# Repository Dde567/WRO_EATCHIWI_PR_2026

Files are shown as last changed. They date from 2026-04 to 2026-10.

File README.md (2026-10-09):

# WRO_EATCHIWI_PR_2026

This repository contains the documentation of the team EatChiwi on the challenge of creating a self-driving vehicle. Here you're going to find all about the creation of the vehicle: mechanical parts, programation, and system thinking. 

Our Ticket to the Internationals! (2026)
===

<div align='center'>
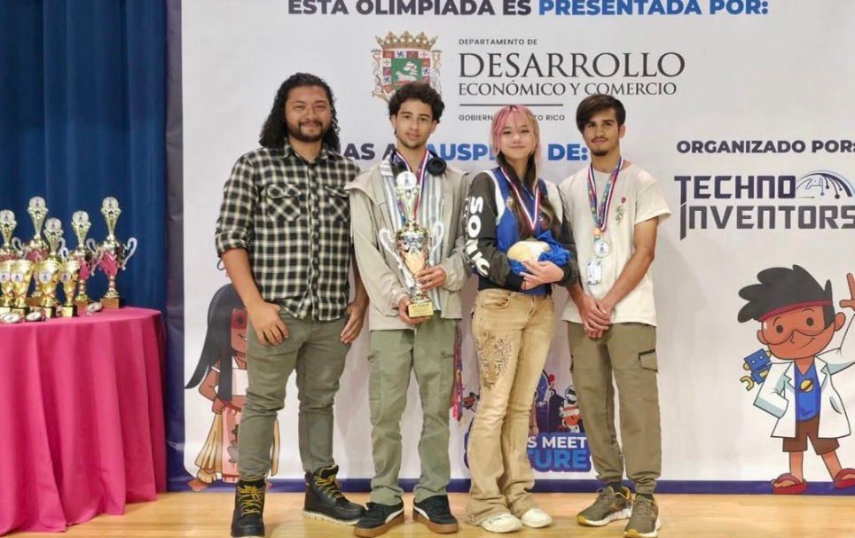
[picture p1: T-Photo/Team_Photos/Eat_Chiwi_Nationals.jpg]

</div>

## Introduction:

Welcome to Team EatChiwi, competing in the Future Engineer's category! Our challenge is to design and program a self-driving car. While building the hardware from scratch wasn't a requirement, we wanted to push our limits. We designed, manufactured, and assembled our entired vehicle from the ground up using 3D printed materials, running on our own custom software. In this process, our dedication was the key to keep pushing forward. In this repository, you'll find our story, our background, and learn more about the whole process of how we create our vehicle. 

<div align='center'>

### <U>[Table of Content!](#table-of-content-)</U>
</div>

Team Photo (from left to right)
===
- Efrain Ortiz (18) - current freshman (college) and our trusted mechanic. Responsible of the creation of the models of the vehicle and the car itself. He's a real innovator and main strategist.
- Faneshka Cartagena (18) - current senior and is the person dedicated to take note of everything. She's a very dedicated and creative person. Responsible of all the documentation of the creating and thinking process. 
- Jose Ortiz (17) - current senior and the programmer of the group. Responsible of the creation of the program of the vehicle and the one in charge to make the strategy come to life.
<div align='center'>
<table>
    <tr> 
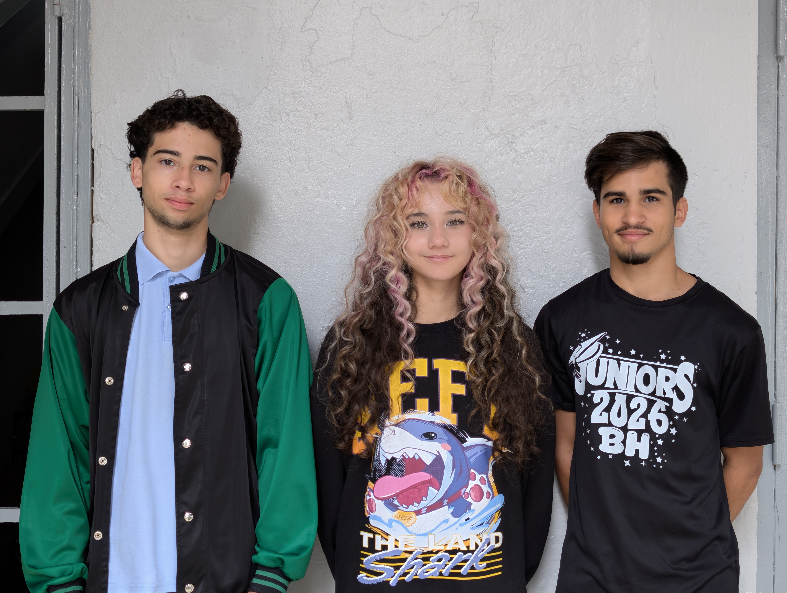
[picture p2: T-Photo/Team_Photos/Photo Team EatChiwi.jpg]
A detailed description of the photo
        <td> 
        </td> 
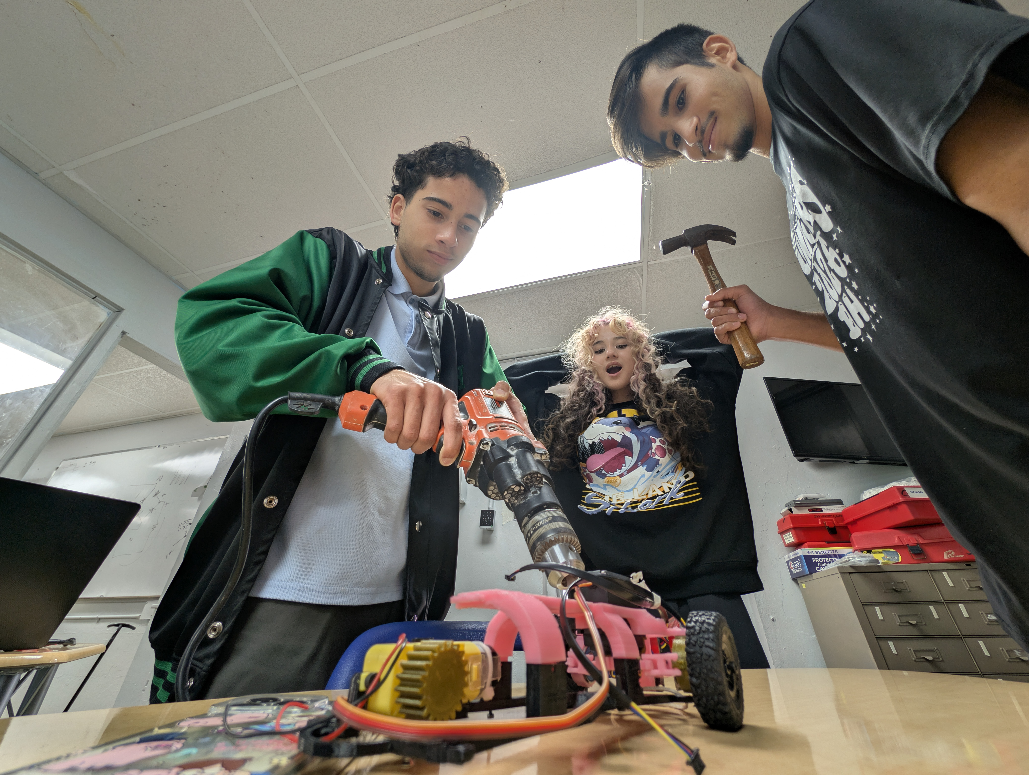
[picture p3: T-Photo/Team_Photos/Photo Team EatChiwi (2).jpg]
        <td> 
        </td>
        </tr>
    </table>
</div>

### <div align='center'> <U> [Learn more about us!](T-Photo\README.md) </U> <div>

Our team's Mascot!
===
Meet our team’s mascot, Chisgüys herself, our lucky charm!
(Ignore what we’re working on in the back.)

<div align='center'>
<table>
    <tr> 
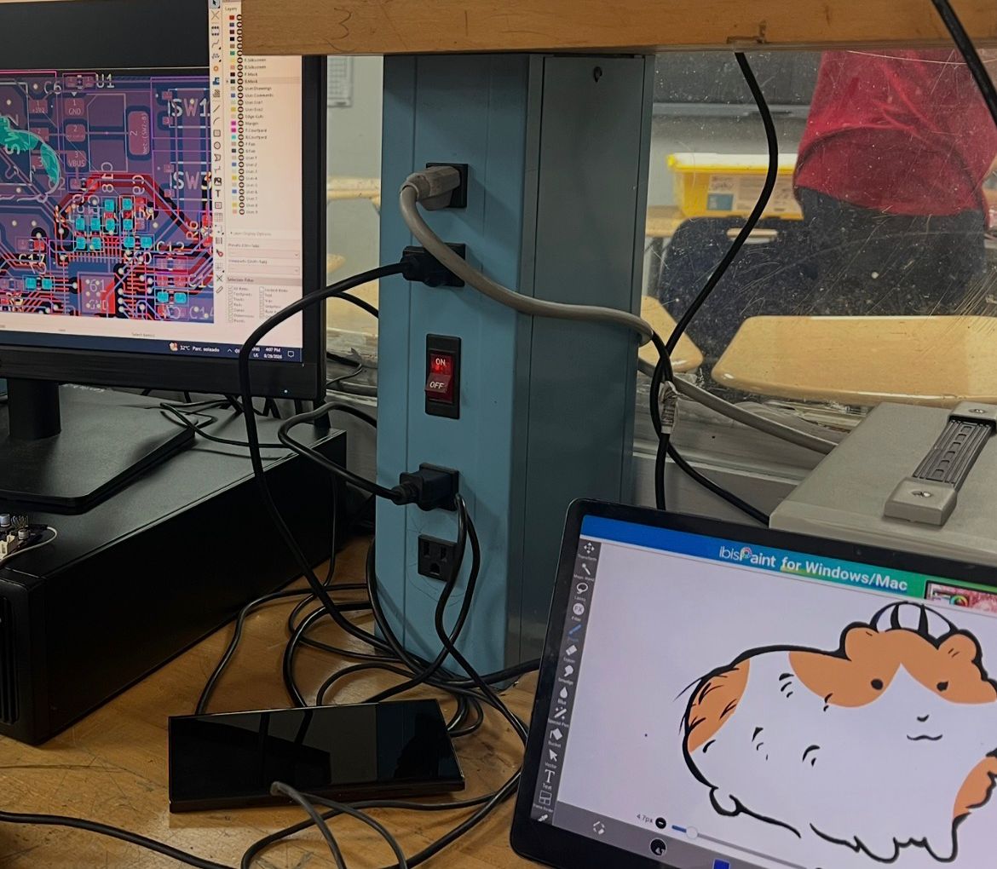
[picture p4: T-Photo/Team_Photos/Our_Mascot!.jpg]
A detailed description of the photo
        <td> 
        </td> 
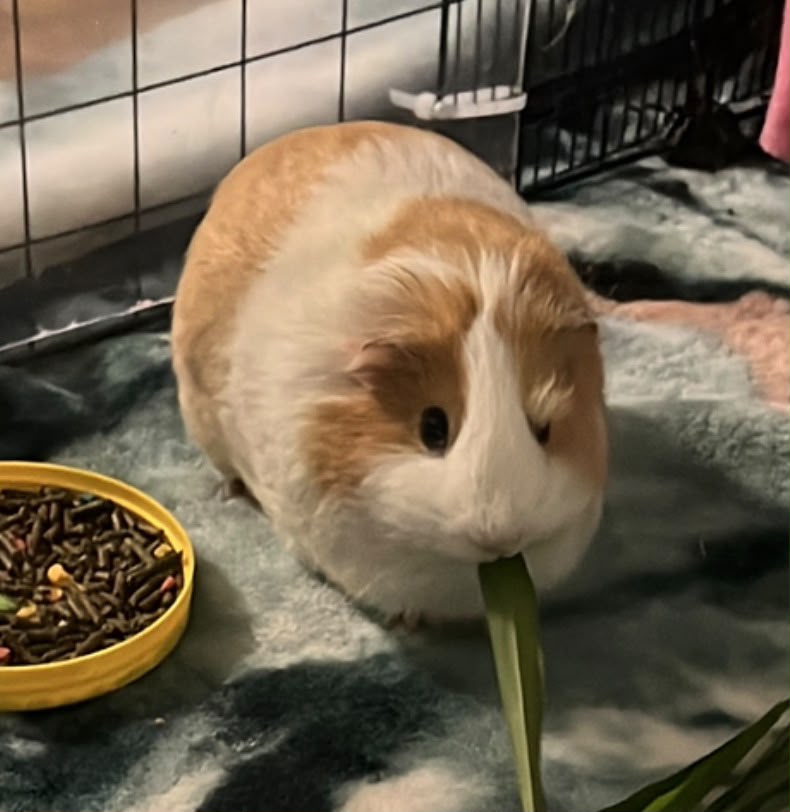
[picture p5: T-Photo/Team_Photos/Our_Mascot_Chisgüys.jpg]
        <td> 
        </td>
        </tr>
    </table>
</div>

Vehicle Photo
===
## V-1.5 (Sept/12/26)
<div align='center'>
<table>
    <tr> 
        <td> <div style="position: relative; display: inline-block;">
        <!-- Image -->
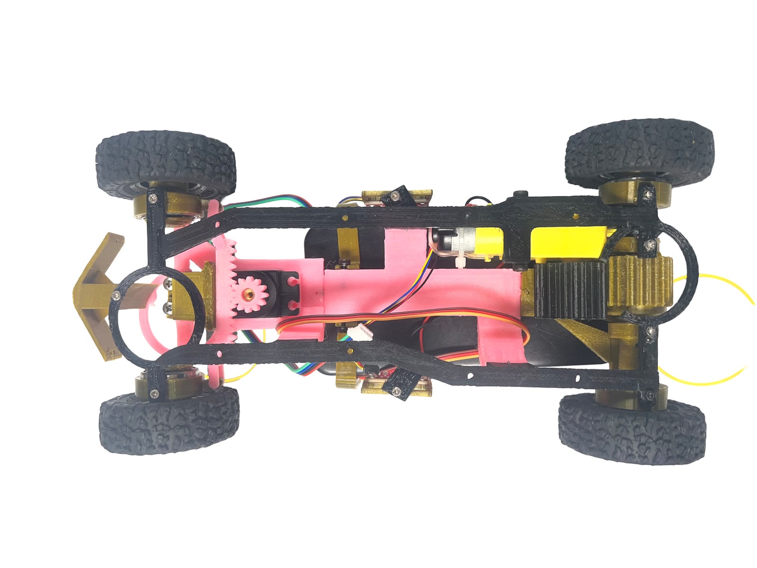
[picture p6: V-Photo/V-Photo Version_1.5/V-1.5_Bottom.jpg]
         
  <!-- The Text Overlay -->
  <div style="
    position: absolute; 
    top: 10px; 
    left: 10px; 
    background-color: rgba(0, 0, 0, 0.79); 
    color: white; 
    padding: 8px 12px; 
    font-family: sans-serif;
    border-radius: 10px;">
    <b> Bottom </b>
  </div>
</div>
        </td> 
        <td> <div style="position: relative; display: inline-block;">
        <!-- Image -->
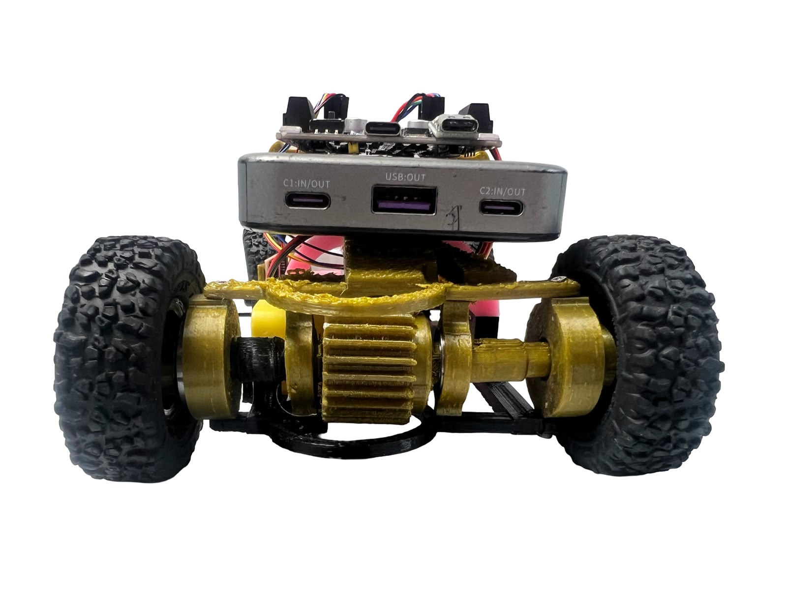
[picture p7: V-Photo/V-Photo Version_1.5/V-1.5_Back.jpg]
         
  <!-- The Text Overlay -->
  <div style="
    position: absolute; 
    top: 10px; 
    left: 10px; 
    background-color: rgba(0, 0, 0, 0.79); 
    color: white; 
    padding: 8px 12px; 
    font-family: sans-serif;
    border-radius: 10px;">
    <b> Back </b>
  </div>
</div>
        </td>
        <td> <div style="position: relative; display: inline-block;">
        <!-- Image -->
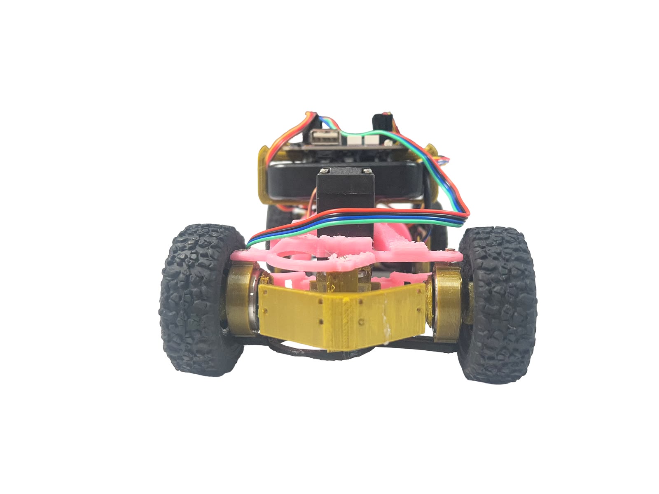
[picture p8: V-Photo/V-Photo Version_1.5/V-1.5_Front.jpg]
         
  <!-- The Text Overlay -->
  <div style="
    position: absolute; 
    top: 10px; 
    left: 10px; 
    background-color: rgba(0, 0, 0, 0.79); 
    color: white; 
    padding: 8px 12px; 
    font-family: sans-serif;
    border-radius: 10px;">
    <b> Front </b>
  </div>
</div>
        </td>
    </tr>
    <tr> 
        <td> <div style="position: relative; display: inline-block;">
        <!-- Image -->
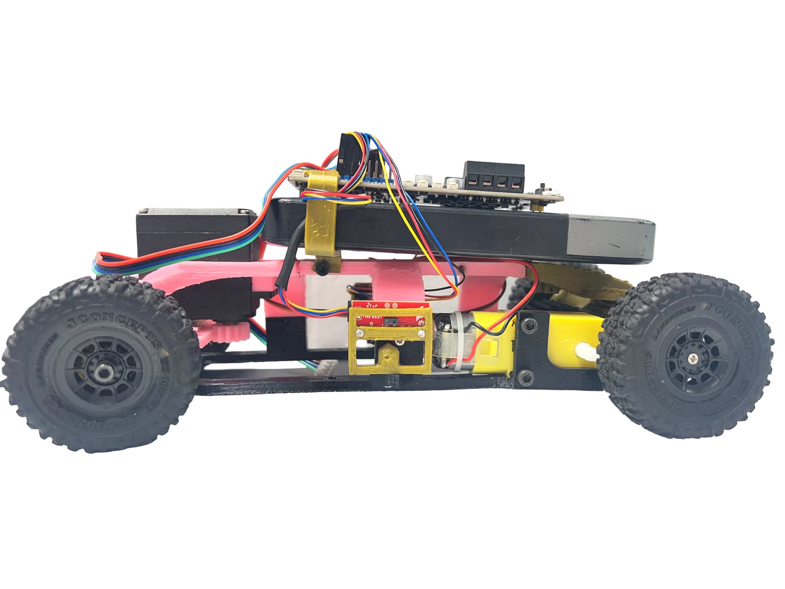
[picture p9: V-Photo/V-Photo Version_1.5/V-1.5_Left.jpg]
         
  <!-- The Text Overlay -->
  <div style="
    position: absolute; 
    top: 10px; 
    left: 10px; 
    background-color: rgba(0, 0, 0, 0.79); 
    color: white; 
    padding: 8px 12px; 
    font-family: sans-serif;
    border-radius: 10px;">
    <b> Left </b>
  </div>
</div>
        </td>
        <td> <div style="position: relative; display: inline-block;">
        <!-- Image -->
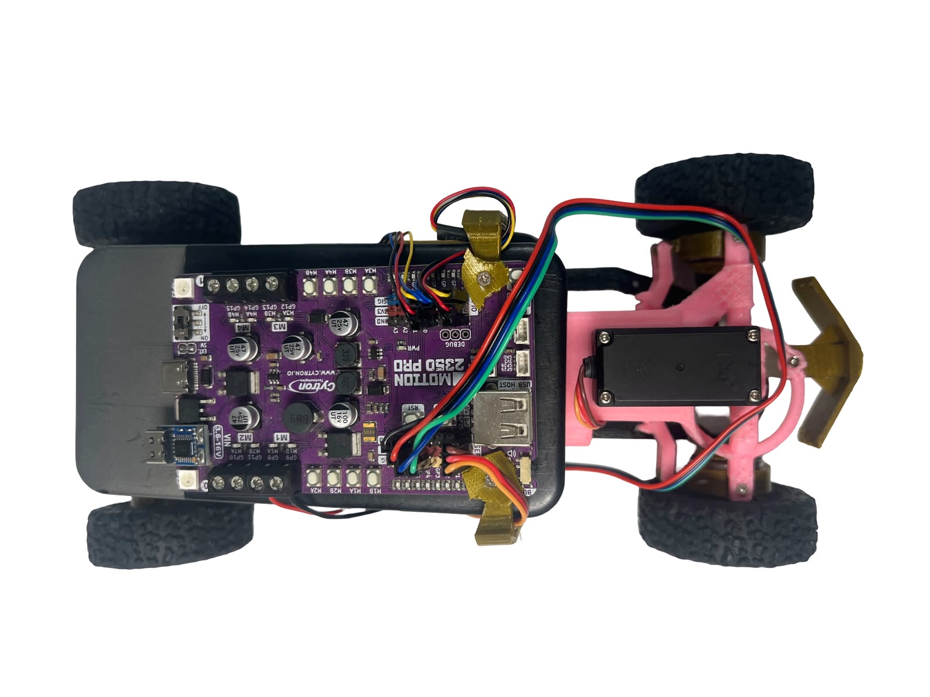
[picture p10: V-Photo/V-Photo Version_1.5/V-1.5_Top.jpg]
         
  <!-- The Text Overlay -->
  <div style="
    position: absolute; 
    top: 10px; 
    left: 10px; 
    background-color: rgba(0, 0, 0, 0.79); 
    color: white; 
    padding: 8px 12px; 
    font-family: sans-serif;
    border-radius: 10px;">
    <b> Top </b>
  </div>
</div>
        </td>
        <td> <div style="position: relative; display: inline-block;">
        <!-- Image -->
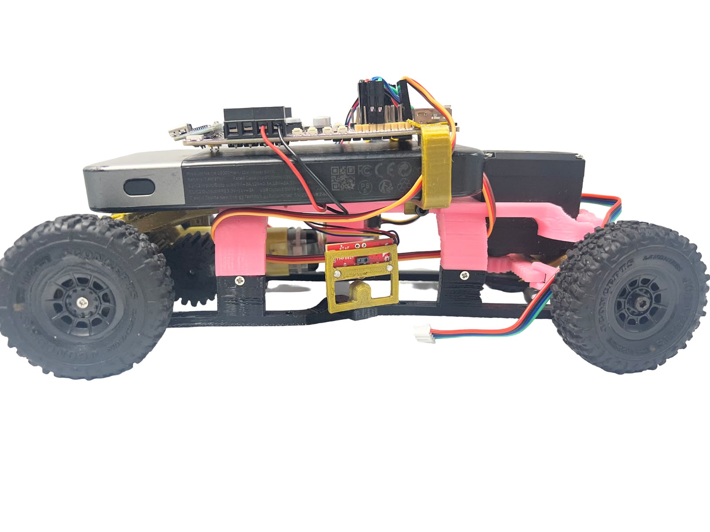
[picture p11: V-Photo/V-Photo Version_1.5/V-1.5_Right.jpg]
         
  <!-- The Text Overlay -->
  <div style="
    position: absolute; 
    top: 10px; 
    left: 10px; 
    background-color: rgba(0, 0, 0, 0.79); 
    color: white; 
    padding: 8px 12px; 
    font-family: sans-serif;
    border-radius: 10px;">
    <b> Right </b>
  </div>
</div>
        </td>
    </tr>
    </table>
  </div>

## About the Mechanics:

The design of the car it's a compact design created in this way to be more quicker to print and more easy to avoid obstacules. The measurements of the car are: lenght = 25cm, width = 11.5cm, tall = 9cm. The car is RWD drived by a TT motor and a MG996r servo motor for steering. The brain of the car is the microcontroller MOTION PRO RP2350. The car counts with 4 wheels of 51mm, 2 TCS3472 on front, 2 TMF8821 on front, TMF8821 sensors on each side and will have a BMI270 for orientation. On the top, just below the microcontroller it's the battery that have a capacity of 37W/h and can supply 35W continuos and counts with a capacity of 10,000mAh.

## About the Code:

Our robot is an autonomous robot programed to complete the Future Engineer's track. To program the robot, the IDE we use is Thonny. To create the code we're using different libraries and sensors:

- `tmf8821` - EJOM CODE @Dde567
- `servo` - EJOM CODE @Dde567
- `dcmotor` - [dcmotor.py](Code-Development/lib/dcmotor.py)
- `tcs3472` - [tcs3472.py](Code-Development/lib/tcs3472.py)

To upload the code to the microcontroller: connect the microcontroller to your computer using a USB cable. Turn it on, then open your IDE (in our case, Thonny) and make sure the microcontroller is recognized. Press the right click on the program you want to upload and select save. Once saved, the code is successfully uploaded to the microcontroller.

## Table of Content :

| Type | Content | Readme |
|---|---|---|
| Mechanics | [CAD](Mechanics/CAD) | [Mobility and Mechanical Design](Mechanics\README.md)|
| Electrical-Design | [Hardware CADS](Electrical-Design/HardwareCADS) / [Electrical Diagram](Electrical-Design/Electrical_Diagram.png) | [Power and Sensor Architecture](Electrical-Design\README.md)|
| Code-Development | [Lib](Code-Development/lib)| [Software Architecture and Obstacle Stategy](Code-Development\README.md) |
| T-Photo | [T-Photo_Normal](T-Photo/Team_Photos/Photo%20Team%20EatChiwi.jpg) / [T-Photo_Crazy](T-Photo\Team_Photos/Photo%20Team%20EatChiwi%20(2).jpg) | [Our Team!](T-Photo/README.md) |
| V-Photo | [V-1.0](V-Photo/V-Photo%20Version_1.0) / [V-1.1](V-Photo/V-Photo%20Version_1.1) / [V-1.2](V-Photo/V-Photo%20Version_1.2) / [V-1.3](V-Photo/V-Photo%20Version_1.3) / [V-1.4](V-Photo/V-Photo%20Version_1.4) / [V-1.5](V-Photo/V-Photo%20Version_1.5)| [Versions of the Car](V-Photo\README.md) |
| Video | [Open Lap for PRNRO 2026 (Team EatChiwi)](https://youtu.be/rVMPH4gbWxk?feature=shared) |||

<div align='center'>

#### <u>[Back to the top!](#wro_eatchiwi_pr_2026)<u>
</div>

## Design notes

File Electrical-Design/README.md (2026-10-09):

# Electrical Design 

In this document you'll find all the things about the electrical components like the capacity of the sensors, the battery, and how is designed the electrical on the robot.

## Introduction
Our electrical design consists of the amount of 8 sensors, with which our car is capable of flawlessly driving through the track without much difficulty. The sensors of our choice are: 2 TCS3472-TMF8821 sensors on the front for effective color detecting and distance reading, some TMF8821 distance sensors on each side for mantaining the car as centered through the track, a HuskyLens 2 camera in the front for better color detection, and lastly our BMI270 IMU which we will use to make the car know where it is at and where is headed to. The powerful brain here is a MOTION PRO RP2350 which programmed in micropython is more than capable of handling every sensor on the list. Our drive hardware consists of the trusty TT motor for driving and a sturdy MG996r servo motor for steering. But this is too simple right? Just using some generic hardware to make our car drive is too basic for us engineers? Well of course, we can do more, we can do better, and thats why we are designing our own sensors for future competitions. As a matter of fact we ALREADY have the schematics for a mix of the powerful TCS and TMF sensors (designed by us) in one board and we plan on making the best hardware we can for our needs in this competence. 

## Battery
The battery it's a JUOVI power bank that has a capacity of 37W/h and can supply 35W continuos, with a capacity of 10,000mAh and includes dual USB Type-C ports and one USB-A port. 

## How much the sensors consume?
- MOTION PRO RP2350 (microcontroller) = Normal Run: Approximately 22mA.

- TMF8821 (distance sensor) = Active Current Consumption: ~57 mA.

- TCS3472 = 235mA to 330mA (operating at 3V)

- BMI270 (accelerometer + gyroscope (MaxODR)) = 685mA

- HuskyLens 2 = 1.5W to 3W (operating at 3.3V or 5.0V)

- MG996r (servo) = Operating Current (Under Load): 500mA - 900mA.

- TT motor = At 6VDC: 160mA @ 250 RPM no-load, and 1.5 Amps when stalled.

## Electrical Diagram 
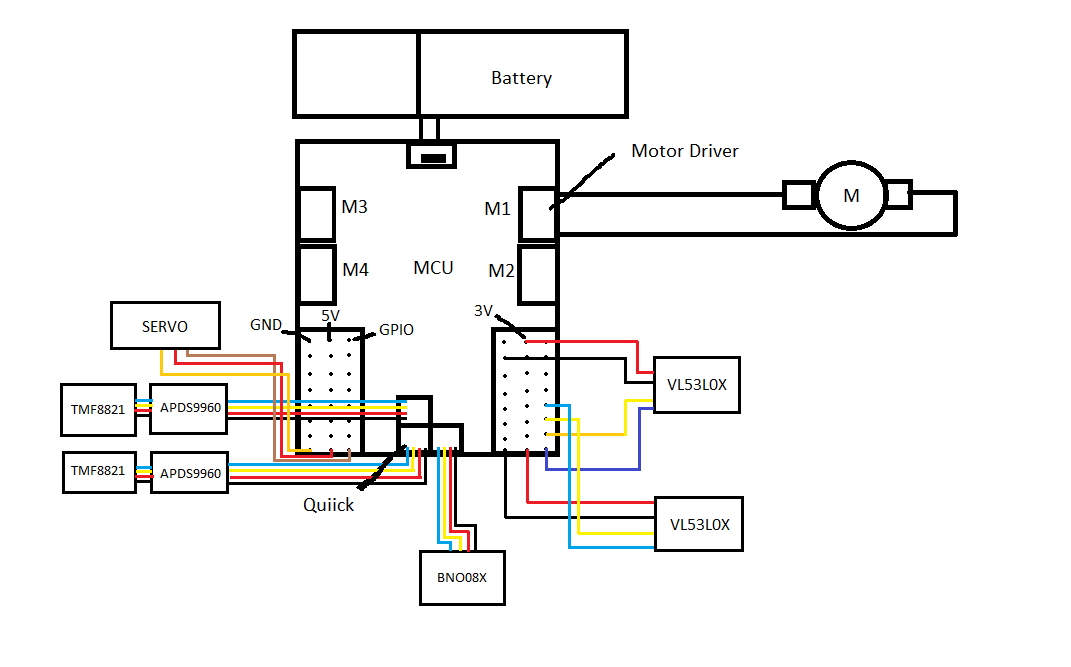
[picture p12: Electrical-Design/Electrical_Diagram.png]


## Robot Composition 

The robot is composed of 8 sensors that are distributed in all the robot. These sensors help the robot to know where he goes, what he have to do, and when he have to stop. Sensors are, in few words, the eyes, hands, and ears of the robot. 

The chosen sensors for the robot were:

| Sensor | Brief Description | Specifications | Library |
|---|---|---|---|
|TMF8821| Distance Sensor | [ams TMF8821 configurable 4x4 multi-time dToF](https://ams-osram.com/products/sensor-solutions/direct-time-of-flight-sensors-dtof/ams-tmf8821-configurable-4x4-multi-zone-time-of-flight-sensor)| [tmf8821.py](Code-Development/lib/tmf8821.py) |
|TCS3472| Color Sensor | [TCS3472 Datasheet](https://cdn-shop.adafruit.com/datasheets/TCS34725.pdf) | [tcs3472.py](Code-Development\lib\tcs3472.py) |
|BMI270| IMU Sensor |  [BMI270 Datasheet](https://www.bosch-sensortec.com/media/boschsensortec/downloads/datasheets/bst-bmi270-ds000.pdf) | [bmi270.py]()
|HuskyLens 2| Advanced Smart AI Vision Sensor | [HuskyLens](https://wiki.dfrobot.com/sen0638/) | [huskylens2.py](Code-Development\lib\pyhuskylens.py)
|Cytron Motion Pro RP2350| Microcontroller | [Cytron Motion Pro RP2350 Datasheet](https://www.cytron.io/p-motion-2350-pro?srsltid=AU7gw4W5Ifi1J22W_zTflltF3oPrDEIvFmEJ27_g_rW_nqw14TCFXhvm)

## Our System!

<table>
  <thead>
    <tr>
      <th width="20%"> Hardware</th>
      <th width="45%"> What it is?</th>
      <th width="45%"> Why we decide to use it
    </tr>
  </thead>
  <tbody>
    <tr>
      <td><b> TMF8821 </b></td>
      <td>
        <details>
          <summary> Description (Click to expand) </summary>
          <p> The ams OSRAM TMF8821 is a compact multi-zone direct Time-of-Flight (dToF) optical sensor measuring precise distances from 10 mm to 5,000 mm at up to 30 Hz. Housed in a tiny 4.6 mm x 2.0 mm x 1.4 mm package, it integrates a 940 nm Class 1 eye-safe VCSEL, a high-sensitivity SPAD array, and on-chip histogram processing to support configurable 3x3, 4x4, or 3x6 grids with a 63° field of view. Communicating over I²C, this high-performance module features sunlight immunity and dynamic cover glass calibration, making it ideal for smartphone laser autofocus, presence detection, and robotics. </p>
        </details>
      </td>
      <td>
      <details>
          <summary> Description (Click to expand) </summary>
          <p> We decide to use the TMF8821 distance sensor for the robot. Why we choose this? Well, after using other distance sensors like the  Vl53l0x and the Vl53l1x (V-1.4 and past versions), or the hcsr04 distance sensor (V-1.3 and past versions), the one who give us better results in reading distance it was the TMF8821. It ensures better lectures than the others, specifically better lectures when its time to read the black walls of the circuit. For this reason, we decided to keep and use the TMF8821 in the robot, seeking for the best lectures and more accuracy. </p>
        </details>
      </td>
    </tr>
    <tr>
      <td><b> TCS3472 </b></td>
      <td>
        <details>
          <summary> Description (Click to expand) </summary>
          <p>The TCS3472 is a high-precision digital color light-to-digital converter featuring a 3×4 photodiode array and four integrated 16-bit analog-to-digital converters for simultaneous RGBC measurement. Equipped with an on-chip infrared blocking filter and an I²C interface, it enables accurate chromaticity analysis and ambient light sensing under varying illumination conditions.</p>
        </details>
      </td>
      <td>
        <details>
          <summary> Description (Click to expand) </summary>
          <p>For the color sensor we decided to use the TCS3472 for the robot. In the past, we were using the APDS9960 (V-1.4 and past versions), but in some tests, we seen that some lectures were not accurate and the robot get confused with the colors, making the computer take bad decisions. Because of this, in this new version we changed to the TCS3472 to secure more accurate lectures. The TCS3472 provide us lecture more precise and that helps the computer to identify the colors faster, precise and take better decisions.</p>
        </details>
      </td>
    </tr>
    <tr>
      <td><b> BMI270 </b></td>
      <td>
        <details>
          <summary> Description (Click to expand) </summary>
          <p> The BMI270 is an ultra-low-power, 6-axis Inertial Measurement Unit (IMU) developed by Bosch Sensortec that combines a 16-bit triaxial accelerometer and a 16-bit triaxial gyroscope into a compact 2.5 x 3.0 mm package. Operating at a low current consumption of approximately 685 µA, it features advanced, on-chip smart motion intelligence for plug-and-play step counting, activity recognition, and wrist gesture detection. Optimized for wearable tech, it is widely used in smartwatches, fitness trackers, hearables, and AR/VR controllers. </p>
        </details>
      </td>
      <td>
        <details>
          <summary> Description (Click to expand) </summary>
          <p> In process </p>
        </details>
      </td>
    </tr>
    <tr>
      <td><b> HuskyLens 2 </b></td>
      <td>
        <details>
          <summary> Description (Click to expand) </summary>
          <p> The HuskyLens 2 is a high-performance edge-AI vision sensor powered by a dual-core RISC-V processor with a 6 TOPS AI accelerator for real-time, on-device image processing without internet or PC dependence. Featuring a 2.4-inch touchscreen and a 60 FPS camera, it supports over 20 pre-installed AI functions—like face recognition, gesture sensing, and line tracking—while seamlessly connecting to Arduino, micro:bit, and Raspberry Pi via I2C/UART. </p>
        </details>
      </td>
      <td>
        <details>
          <summary> Description (Click to expand) </summary>
          <p> In one of our brainstormings, the idea of use a camare surge, and, with this, the doubt of use or not use a camera stay there for a long time. One day one of our members appeared with the HuskyLens 2, and since we already had it, why not use it. The HuskyLens 2 provide us exceptional features like line tracking, color detection, object detection, and other features that can be really useful to complete all the challenges. As a result, we decide to improve and add this complex camera to our robot, to make sure the decisions would be flawless. </p>
        </details>
      </td>
    </tr>
    <tr>
      <td><b> Cytron Motion Pro RP2350 </b></td>
      <td>
        <details>
          <summary> Description (Click to expand) </summary>
          <p> The Cytron MOTION 2350 Pro is a beginner-friendly robotics controller powered by the dual-core Raspberry Pi RP2350 microcontroller, operating between 3.6V and 16V. Designed for rapid prototyping, it drives up to 4 brushed DC motors (3A continuous/5A peak) and 8 servos, while featuring 3 Maker Ports, an onboard USB-A host port for gamepads, and physical quick-test buttons for no-code hardware testing. It comes preloaded with CircuitPython and fully supports MicroPython, C/C++, and Arduino IDE, making it a highly accessible all-in-one solution for building mobile robots and smart hardware projects. </p>
        </details>
      </td>
      <td>
        <details>
          <summary> Description (Click to expand) </summary>
          <p> Of all the microcontroller we could have choosen, we decided to go with the Cytron Motion Pro RP2350. This microcontroller provide us more than we need; it's a fast, precise, and easy to use microcontroller, guaranteeing us that all the information would be processed and analyzed to take the refined decisions. </p>
        </details>
      </td>
    </tr>
  </tbody>
</table>

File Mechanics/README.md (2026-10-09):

# Mechanical Engineer

In this document you'll find all the things related to the mechanical engineer like the mobility system, components of the car, and others.

## About Our Car

The design of the car was made on computer using Fusion, an 3D designer app. The designs of the car were made thinking on been compact. Why? Well because if the car is smaller, can avoid obstacules more easily. All the parts that make up the car (chassis, mechanics, axles, etc.) were designed by our trusted mechanical engineer Efraín Ortiz. All the parts designed were printed using PETG and PLA filaments with the Creality 3 v3 ke and Dremel 3d45rinte prs. The chassis of the car is an squeletical design to be quicker to print, modify or change anything in case of be needed. The measurements of the car are: lenght = 25cm, width = 11.5cm, tall = 9cm. The car is RWD drived by a trusty TT motor and a MG996r servo motor for steering. The brain of the car consists of the microcontroller MOTION PRO RP2350 which is a versatile 30 programmable pin board capable of more than what we need it for. The car counts with 4 wheels of 51mm diameter, 2 TCS3472 color sensors on front for a wider detecting range, 2 TMF8821 sensors on the front to read distance, TMF8821 sensors for read distance on each side, a HuskyLens 2 camera for better color detection, and a BMI270 for orientation and acceleration. On the top just below the microcontroller is the battery, this it's a JUOVI power bank that have a capacity of 37W/h and can supply 35W continuos, with a capacity of 10,000mAh and includes dual USB Type-C ports and one USB-A port. 

## Current Model Photos (V-1.5)
<div align='center'>
<table>
    <tr> 
        <td> <div style="position: relative; display: inline-block;">
        <!-- Image -->
         Accessibility description
  <!-- The Text Overlay -->
  <div style="
    position: absolute; 
    top: 10px; 
    left: 10px; 
    background-color: rgba(0, 0, 0, 0.79); 
    color: white; 
    padding: 8px 12px; 
    font-family: sans-serif;
    border-radius: 10px;">
    <b> Bottom </b>
  </div>
</div>
        </td> 
        <td> <div style="position: relative; display: inline-block;">
        <!-- Image -->
         Accessibility description
  <!-- The Text Overlay -->
  <div style="
    position: absolute; 
    top: 10px; 
    left: 10px; 
    background-color: rgba(0, 0, 0, 0.79); 
    color: white; 
    padding: 8px 12px; 
    font-family: sans-serif;
    border-radius: 10px;">
    <b> Back </b>
  </div>
</div>
        </td>
        <td> <div style="position: relative; display: inline-block;">
        <!-- Image -->
         Accessibility description
  <!-- The Text Overlay -->
  <div style="
    position: absolute; 
    top: 10px; 
    left: 10px; 
    background-color: rgba(0, 0, 0, 0.79); 
    color: white; 
    padding: 8px 12px; 
    font-family: sans-serif;
    border-radius: 10px;">
    <b> Front </b>
  </div>
</div>
        </td>
    </tr>
    <tr> 
        <td> <div style="position: relative; display: inline-block;">
        <!-- Image -->
         Accessibility description
  <!-- The Text Overlay -->
  <div style="
    position: absolute; 
    top: 10px; 
    left: 10px; 
    background-color: rgba(0, 0, 0, 0.79); 
    color: white; 
    padding: 8px 12px; 
    font-family: sans-serif;
    border-radius: 10px;">
    <b> Left </b>
  </div>
</div>
        </td>
        <td> <div style="position: relative; display: inline-block;">
        <!-- Image -->
         Accessibility description
  <!-- The Text Overlay -->
  <div style="
    position: absolute; 
    top: 10px; 
    left: 10px; 
    background-color: rgba(0, 0, 0, 0.79); 
    color: white; 
    padding: 8px 12px; 
    font-family: sans-serif;
    border-radius: 10px;">
    <b> Top </b>
  </div>
</div>
        </td>
        <td> <div style="position: relative; display: inline-block;">
        <!-- Image -->
         Accessibility description
  <!-- The Text Overlay -->
  <div style="
    position: absolute; 
    top: 10px; 
    left: 10px; 
    background-color: rgba(0, 0, 0, 0.79); 
    color: white; 
    padding: 8px 12px; 
    font-family: sans-serif;
    border-radius: 10px;">
    <b> Right </b>
  </div>
</div>
        </td>
    </tr>
    </table>
  </div>

## How it is built?

On top is the microcontroller MOTION PRO RP2350 and below of it is the battery. Before the front part is located the TT motor and the MG996r servo motor for steering, and on top of it is located the BMI270 for the orientation. On both sides the car counts with the TMF8821 sensor to read distance. On the front the car counts with 2 TCS3472 for color reading and 2 TMF8821 for distance reading.

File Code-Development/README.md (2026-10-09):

# Code Explanation 

 In this document you'll find all the explanation of the code, system thinking and decision making.

## About the Code 

The robot's code is designed so that it can complete all the challenges of the WRO Future Engineers 2026 competition circuit. This code was created on Thonny, an IDE for Phyton and in this case, used for microphyton. The microcontroller we used is the MOTION PRO RP2350.

## The Code 

The code itself begins like this: at the start, it imports all the libraries. After that, it sets up the communication channels and the buttons, along with other functions. Then, the robot verifies the communication channels before defining the different sensors and functions.

After that, the code starts creating and defining the functions, as well as calculating or compensating values. Once this is done, the robot begins running, centering the wheels and reading all the data in order to calculate where it will move and how much it will move.

## System Thinking 

The robot’s critical thinking works like this: at the beginning, the robot reads everything to determine where it is located and where it needs to move. Then, it starts moving forward to detect a larger distance. This is because the robot checks both distances and moves toward the one with the greater value, since that indicates more open space (in other words, not a wall). For example, if the left distance sensor detects a greater distance than the right one, the robot will move to the left.

After moving in the corresponding direction, the robot will center itself by reading both distances and calculating an average so it can stay in the middle. To verify that it moved in the correct direction, the robot uses an orientation sensor, which indicates how many degrees it has turned and whether it is moving straight or in a curve.

The robot will also detect any walls in front of it and stop before crashing. If it detects a wall ahead, it will reverse for approximately 1 to 1.5 seconds. This would be the full behavior on a track without obstacles.

On a track with obstacles, the robot follows the same logic, but additionally uses the front distance sensors while it is between two walls (it determines this when both distances are similar and the average is not very large). If the robot detects an object, it will approach it to identify its color. If the obstacle is red, the robot will pass on the right side of the block; if it is green, it will pass on the left side.
To know when it has completed three laps, the robot keeps count of how many times it detects a larger distance or how many times it turns in a certain direction. In total, there would be 12 turns, since the track is square and each lap represents 4 turns.

## Recent Changes

- VL53L0X for TMF8821
- APDS9960 for TCS3472
- BNO085 for BMI270

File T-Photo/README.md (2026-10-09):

# Our Extraordinary Team!

Hi! We are the team EatChiwi, a team of three students of the Vocational Superior School Benjamin Harrison of Cayey. We are a dedicated team that is participating on the WRO 2026 competition on the category of Future Engineer's.

 <table>
    <tr> 
        <td> 
        </td> 
        <td> 
        </td>
        </tr>
    </table>

## How the team was formed?

The team EatChiwi was formed in an unexpected way, starting with how the members came together:

- Efraín J. Ortiz Mulero was already participating in the Future Engineer category and had a solid amount of experience in both mechanics and programming. He is also the brother of José F. Ortiz Mulero, who later joined the Future Engineer category.

- José had previously participated in RoboMission, where he served as both the mechanic and programmer for his team. He was very dedicated to his work and constantly sought growth, which led him to join Future Engineer. Being teamed up with someone he already knew and lived with made this an even better opportunity. 

- Faneshka Cartagena Maldonado was participating in RoboSports, where she worked as an engineer, programmer, and in charge of documentation for her team. At one point, one of her teammates left their all girls group, leaving her with just one remaining teammate, who eventually left as well. This situation led her to explore new opportunities, and she decided to join the Future Engineer category. Since the team only needed one more member to be complete, she became the perfect addition.

 The three of them already knew each other well, which helped everything come together naturally. As for the name “EatChiwi”, it comes from Faneshka’s guinea pig, named Chiwi. Efraín thought it would be funny to name the team EatChiwi, since they often joked about how guinea pigs are eaten in some cultures.
 
 The team roles were assigned based on each member’s strengths: Efraín took on the role of mechanic, as he excelled with the 3D printer and designs, Faneshka became responsible for documentation because of her strong note taking skills, and José focused on programming, as he worked best with coding and learned quickly.

 ## A Bit of Our Experience on Robotics:

### Efraín Josue Ortiz Mulero:

<div align='center'>
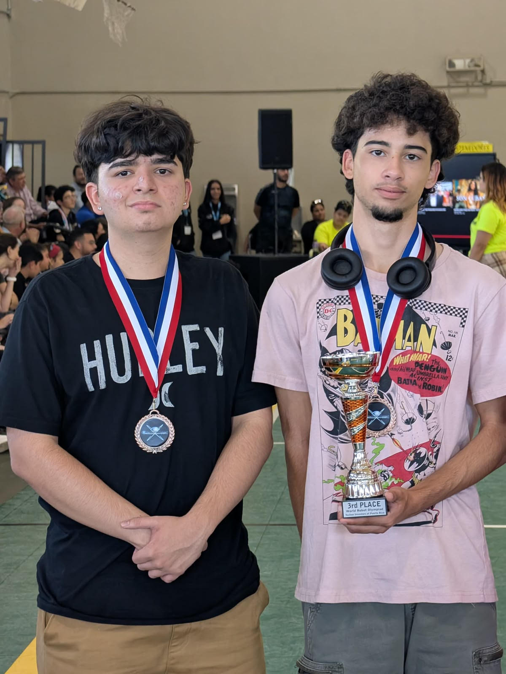
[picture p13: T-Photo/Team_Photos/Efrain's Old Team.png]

</div>

I participated in RoboSports for a brief period in 2024 as a substitute. Later that same year, I joined Future Engineers and participated in the 2024 Open Championship in Puerto Rico, where we placed 4th.

During 2024, I was the mechanical and electrical engineer for the vehicle. I was responsible for different aspects of the vehicle’s construction, design, and electrical systems.

Our current team was formed after a selection of the best members of the club, which was decided by the coach and me. The previous team was not performing as expected, so we decided to make a change and form a new team for Future Engineers.

Currently, I continue to be the mechanical and electrical engineer for the vehicle. I mainly work on the mechanical and electrical aspects of the autonomous car, including its construction, design, and overall functionality. Right now, we are also preparing to represent Puerto Rico on December 7 at the upcoming competition.

### José Fabian Ortiz Mulero:

<div align='center'>
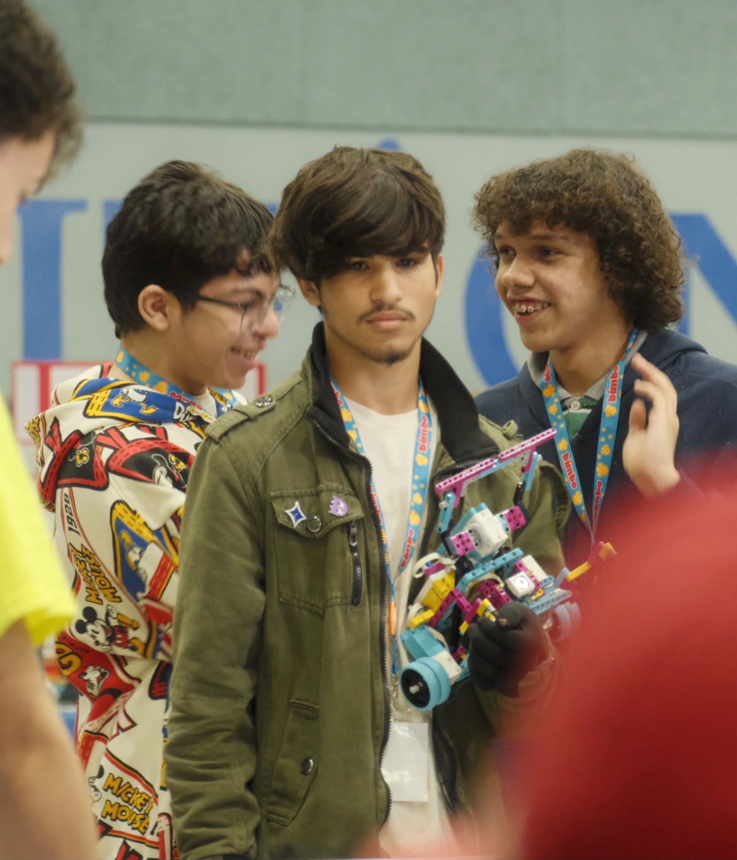
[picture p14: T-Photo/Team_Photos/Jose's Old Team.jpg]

</div>

 My name is José F. Ortiz Mulero, and I joined the robotics club during 10th grade. I decided to join because I had already developed an interest in robotics, and since my brother was already part of the club, I saw it as an opportunity to expand my knowledge and develop new skills.

The category I joined was Robot Mission Senior. Since it was the only category with an open spot, I decided to take the opportunity. I ended up becoming the mechanic on my team, but I also participated and learned about the other areas of the team. Through this experience, I gained valuable knowledge about robotics, teamwork, problem-solving, and responsibility.

My team worked hard and eventually competed at the national level, where we placed 2nd. This achievement gave us the opportunity to travel to Singapore and represent Puerto Rico at the international competition. Being able to compete internationally was an incredible experience and motivated me to continue growing in robotics.

After that, another opportunity came along that allowed me to continue developing my skills and pursue my interest in becoming a future engineer. I joined the same team as my brother and one of my friends, but this time I took on a new role as the programmer. This has allowed me to learn even more about robotics, programming, and how the different parts of a robot work together.

Now, we are looking forward to another important opportunity: representing Puerto Rico in this category this December. I am excited to continue learning, improving my skills, and giving my best alongside my teammates.

### Faneshka Cartagena Maldonado:

<div align='center'>
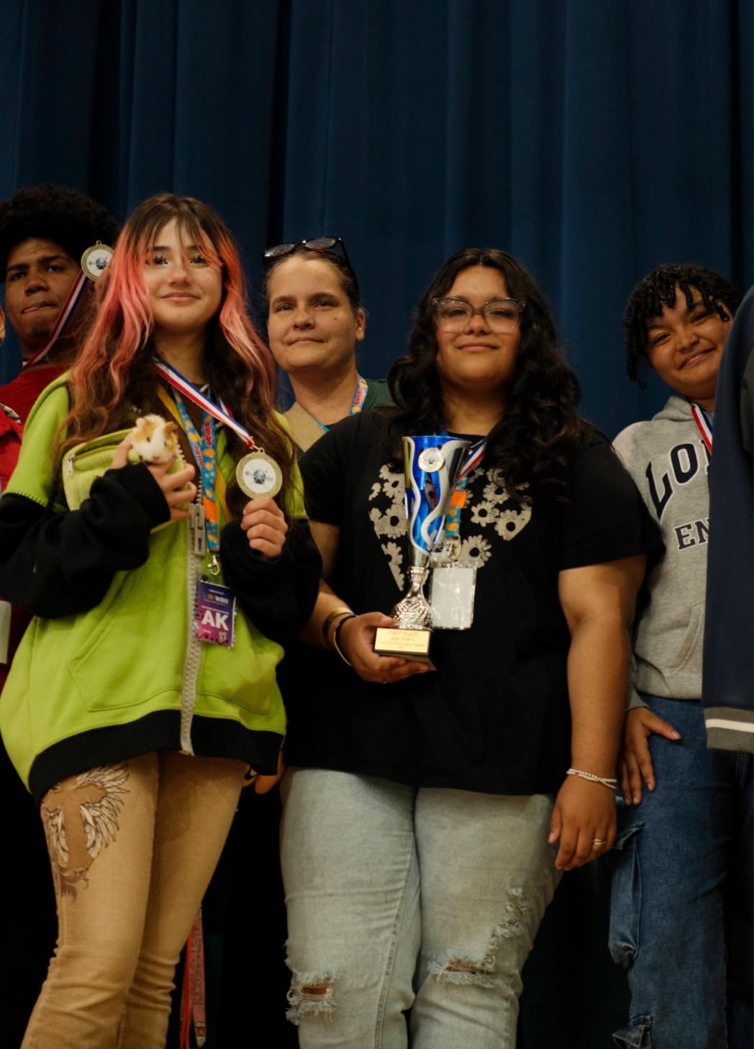
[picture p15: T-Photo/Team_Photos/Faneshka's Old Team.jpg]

</div>

My name is Faneshka Cartagena Maldonado. I joined the robotics club during 10th grade. I joined the robotics club because one of my mutual friends was interested in the club, and I wanted to understand why it was so special to them. Soon, I found out why. This whole process was new to me since I didn’t really have an interest in robotics before joining.

I had an open spot in RoboSports, and I was placed on a team that had already competed in 2024 and had the opportunity to travel to Turkey. At first, my role was to document things and sketch the models. Later, the team went through some changes, and I became the mechanic while also being present and helping in the other areas of the team. The team also got a new name, Sirens.

With Sirens, we went to Nationals and placed first. We then had the opportunity to go to an international competition, where my team traveled and represented Puerto Rico. After that, my team eventually broke apart, leaving me looking for another opportunity to continue growing in robotics.

That is when I saw an opportunity with Future Engineers and decided to take it. I found two of my friends there as well, which made the experience even better. I also took on a new role. This time, I became the person responsible for documenting our work, and I was also the one who created our team logo.

We went on to win first place at Nationals, and now we are looking forward to representing Puerto Rico in this category. I am excited to continue learning, growing, and gaining more experience through robotics while representing Puerto Rico alongside my teammates.

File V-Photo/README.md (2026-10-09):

# Vehicle Models 
  In this document are all the physical versions of the vehicle and a short description of each model.
 
 ## V-1.0 (Feb/21/26)
This design was made using 3D printing. It is a small vehicle that has an ultrasonic sensor to detect when it should turn the front wheels. On top of the robot, the battery is located, and above that is the Maker Pi controller, which processes all the data. This model doesn't detect colors.

<table>
    <tr> 
        <td> <div style="position: relative; display: inline-block;">
        <!-- Image -->
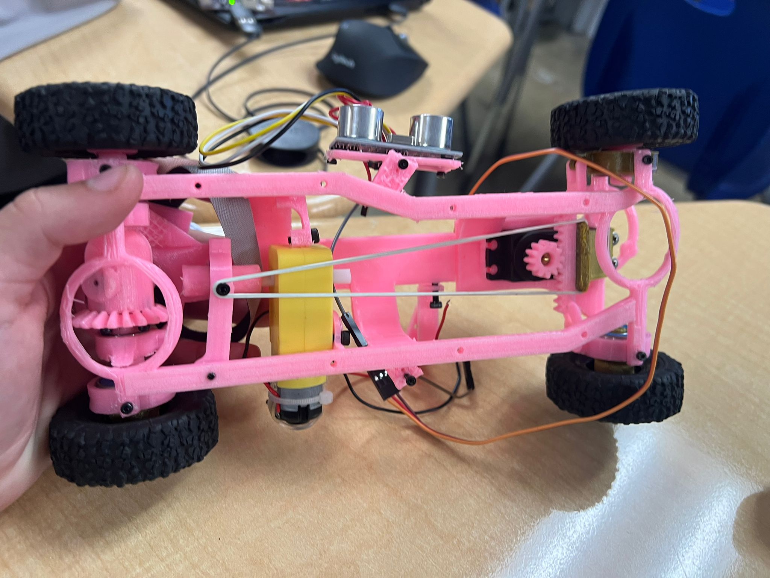
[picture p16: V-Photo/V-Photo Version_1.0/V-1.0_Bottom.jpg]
         
  <!-- The Text Overlay -->
  <div style="
    position: absolute; 
    top: 10px; 
    left: 10px; 
    background-color: rgba(0, 0, 0, 0.79); 
    color: white; 
    padding: 8px 12px; 
    font-family: sans-serif;
    border-radius: 10px;">
    <b> Bottom </b>
  </div>
</div>
        </td> 
        <td> <div style="position: relative; display: inline-block;">
        <!-- Image -->
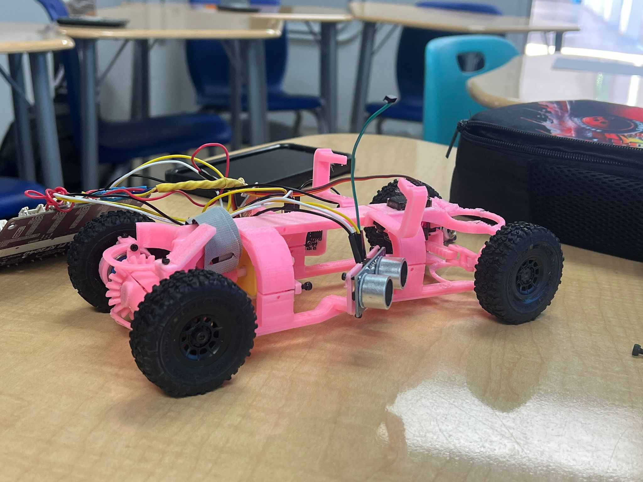
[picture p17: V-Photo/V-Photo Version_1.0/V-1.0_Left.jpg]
         
  <!-- The Text Overlay -->
  <div style="
    position: absolute; 
    top: 10px; 
    left: 10px; 
    background-color: rgba(0, 0, 0, 0.79); 
    color: white; 
    padding: 8px 12px; 
    font-family: sans-serif;
    border-radius: 10px;">
    <b> Left </b>
  </div>
</div>
        </td>
    <tr>
        <td> <div style="position: relative; display: inline-block;">
        <!-- Image -->
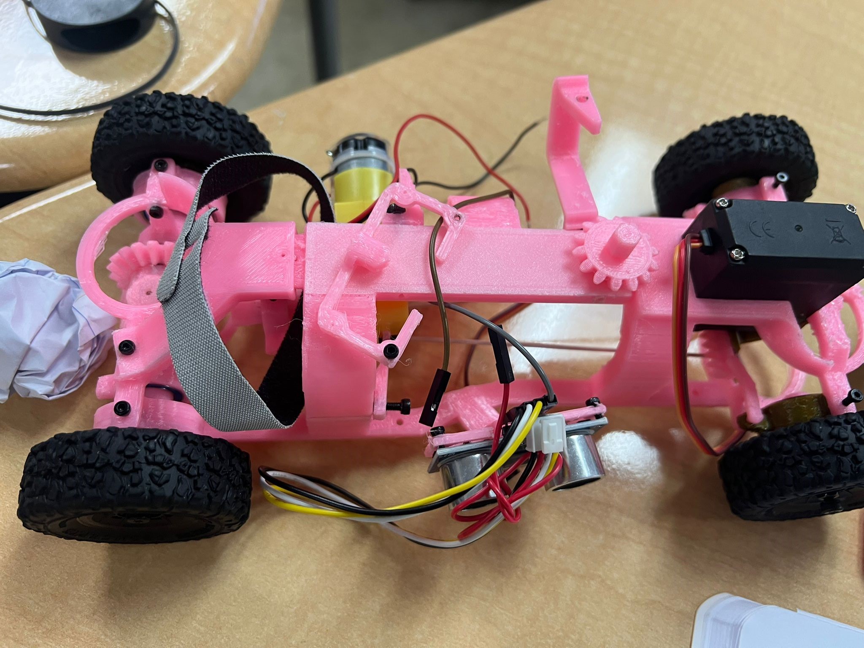
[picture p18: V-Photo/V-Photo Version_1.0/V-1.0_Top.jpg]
         
  <!-- The Text Overlay -->
  <div style="
    position: absolute; 
    top: 10px; 
    left: 10px; 
    background-color: rgba(0, 0, 0, 0.79); 
    color: white; 
    padding: 8px 12px; 
    font-family: sans-serif;
    border-radius: 10px;">
    <b> Top </b>
  </div>
</div>
        </td>
        </td>
        <td> <div style="position: relative; display: inline-block;">
        <!-- Image -->
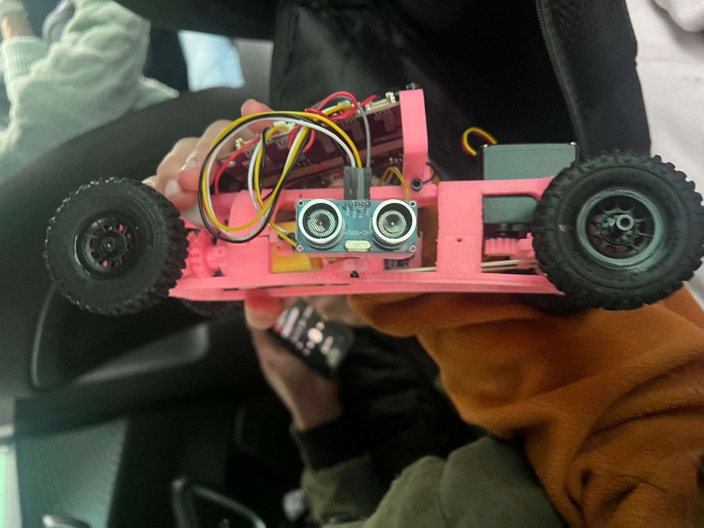
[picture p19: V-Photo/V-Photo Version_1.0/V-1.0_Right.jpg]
         
  <!-- The Text Overlay -->
  <div style="
    position: absolute; 
    top: 10px; 
    left: 10px; 
    background-color: rgba(0, 0, 0, 0.79); 
    color: white; 
    padding: 8px 12px; 
    font-family: sans-serif;
    border-radius: 10px;">
    <b> Right </b>
  </div>
</div>
        </td>
    </tr>
    </table>

## V-1.1 (Mar/28/26)
 This model is made using 3D-printed materials and is very similar to the previous design. It includes an ultrasound sensor on the left side, although it is not programmed yet.

This version uses a different differential, which is larger than the one in the previous design. On top of the vehicle, the battery is mounted along with the Maker Pi controller, where all the robot’s data is processed. Overall, this model is a simpler version of the design.

<table>
    <tr> 
        <td> <div style="position: relative; display: inline-block;">
        <!-- Image -->
         Accessibility description
  <!-- The Text Overlay -->
  <div style="
    position: absolute; 
    top: 10px; 
    left: 10px; 
    background-color: rgba(0, 0, 0, 0.79); 
    color: white; 
    padding: 8px 12px; 
    font-family: sans-serif;
    border-radius: 10px;">
    <b> Bottom </b>
  </div>
</div>
        </td> 
        <td> <div style="position: relative; display: inline-block;">
        <!-- Image -->
         Accessibility description
  <!-- The Text Overlay -->
  <div style="
    position: absolute; 
    top: 10px; 
    left: 10px; 
    background-color: rgba(0, 0, 0, 0.79); 
    color: white; 
    padding: 8px 12px; 
    font-family: sans-serif;
    border-radius: 10px;">
    <b> Front </b>
  </div>
</div>
        </td>
        <td> <div style="position: relative; display: inline-block;">
        <!-- Image -->
         Accessibility description
  <!-- The Text Overlay -->
  <div style="
    position: absolute; 
    top: 10px; 
    left: 10px; 
    background-color: rgba(0, 0, 0, 0.79); 
    color: white; 
    padding: 8px 12px; 
    font-family: sans-serif;
    border-radius: 10px;">
    <b> Back </b>
  </div>
</div>
        </td>
    </tr>
    <tr> 
        <td> <div style="position: relative; display: inline-block;">
        <!-- Image -->
         Accessibility description
  <!-- The Text Overlay -->
  <div style="
    position: absolute; 
    top: 10px; 
    left: 10px; 
    background-color: rgba(0, 0, 0, 0.79); 
    color: white; 
    padding: 8px 12px; 
    font-family: sans-serif;
    border-radius: 10px;">
    <b> Left </b>
  </div>
</div>
        </td>
        <td> <div style="position: relative; display: inline-block;">
        <!-- Image -->
         Accessibility description
  <!-- The Text Overlay -->
  <div style="
    position: absolute; 
    top: 10px; 
    left: 10px; 
    background-color: rgba(0, 0, 0, 0.79); 
    color: white; 
    padding: 8px 12px; 
    font-family: sans-serif;
    border-radius: 10px;">
    <b> Top </b>
  </div>
</div>
        </td>
        <td> <div style="position: relative; display: inline-block;">
        <!-- Image -->
         <img src="V-Photo Version_1.1\V-1.1_Right.jpg" width ="400" height ="300"" alt="Accessibility description" width ="400" height ="300" style="display: block;">
  <!-- The Text Overlay -->
  <div style="
    position: absolute; 
    top: 10px; 
    left: 10px; 
    background-color: rgba(0, 0, 0, 0.79); 
    color: white; 
    padding: 8px 12px; 
    font-family: sans-serif;
    border-radius: 10px;">
    <b> Right </b>
  </div>
</div>
        </td>
    </tr>
    </table>

## V-1.2 (Apr/10/26)
This model is made using 3D printing materials. It includes a distant sensor (vl53l0x) located on the left side of the model. The chassis has been redesigned because we changed the differential model, which required adjustments to the overall structure. On the top, you can see the battery, and above it is the Cytron Motion RP2350 Pro, where all the data is processed. At the front, there are two TMF8821 sensors used for distance detection, which are not programmed at the moment.

<table>
    <tr> 
        <td> <div style="position: relative; display: inline-block;">
        <!-- Image -->
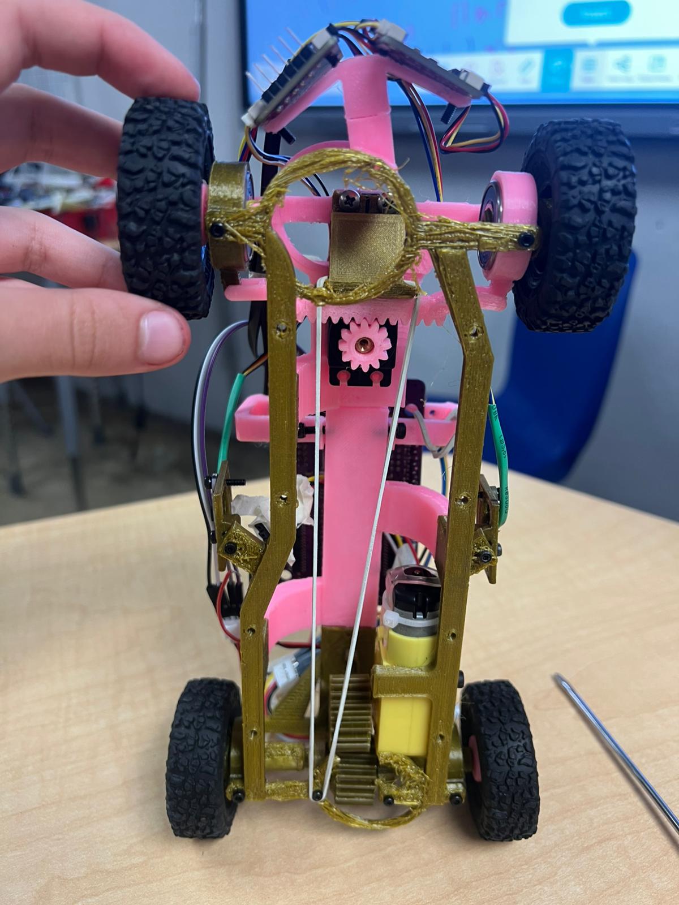
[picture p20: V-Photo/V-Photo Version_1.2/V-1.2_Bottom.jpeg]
         
  <!-- The Text Overlay -->
  <div style="
    position: absolute; 
    top: 10px; 
    left: 10px; 
    background-color: rgba(0, 0, 0, 0.79); 
    color: white; 
    padding: 8px 12px; 
    font-family: sans-serif;
    border-radius: 10px;">
    <b> Bottom </b>
  </div>
</div>
        </td> 
        <td> <div style="position: relative; display: inline-block;">
        <!-- Image -->
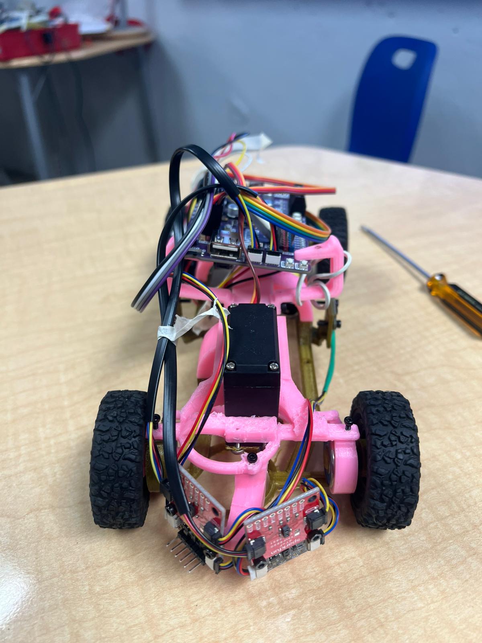
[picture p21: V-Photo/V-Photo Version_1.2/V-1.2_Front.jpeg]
         
  <!-- The Text Overlay -->
  <div style="
    position: absolute; 
    top: 10px; 
    left: 10px; 
    background-color: rgba(0, 0, 0, 0.79); 
    color: white; 
    padding: 8px 12px; 
    font-family: sans-serif;
    border-radius: 10px;">
    <b> Front </b>
  </div>
</div>
        </td>
        <td> <div style="position: relative; display: inline-block;">
        <!-- Image -->
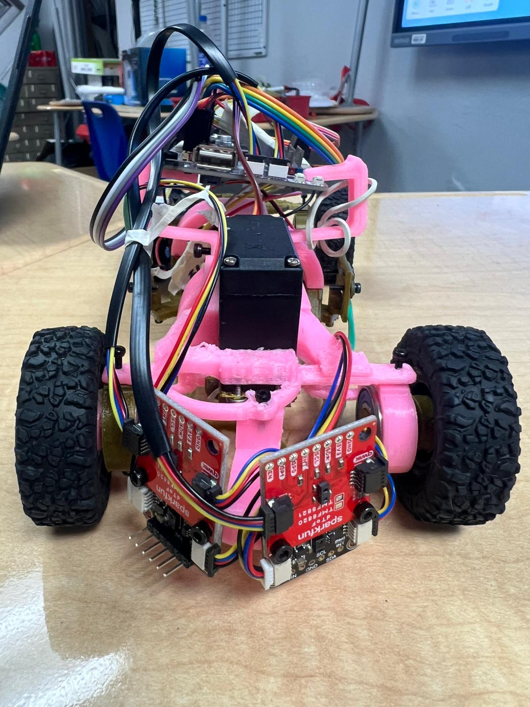
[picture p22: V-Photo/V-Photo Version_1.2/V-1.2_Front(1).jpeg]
         
  <!-- The Text Overlay -->
  <div style="
    position: absolute; 
    top: 10px; 
    left: 10px; 
    background-color: rgba(0, 0, 0, 0.79); 
    color: white; 
    padding: 8px 12px; 
    font-family: sans-serif;
    border-radius: 10px;">
    <b> Front(2) </b>
  </div>
</div>
        </td>
    </tr>
    <tr> 
        <td> <div style="position: relative; display: inline-block;">
        <!-- Image -->
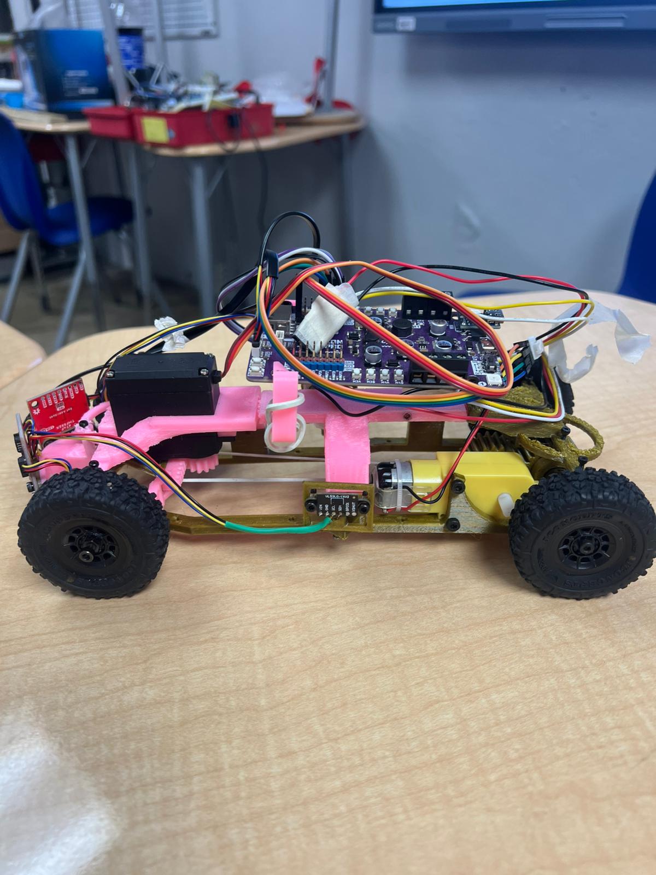
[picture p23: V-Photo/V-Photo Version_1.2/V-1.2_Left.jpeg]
         
  <!-- The Text Overlay -->
  <div style="
    position: absolute; 
    top: 10px; 
    left: 10px; 
    background-color: rgba(0, 0, 0, 0.79); 
    color: white; 
    padding: 8px 12px; 
    font-family: sans-serif;
    border-radius: 10px;">
    <b> Left </b>
  </div>
</div>
        </td>
        <td> <div style="position: relative; display: inline-block;">
        <!-- Image -->
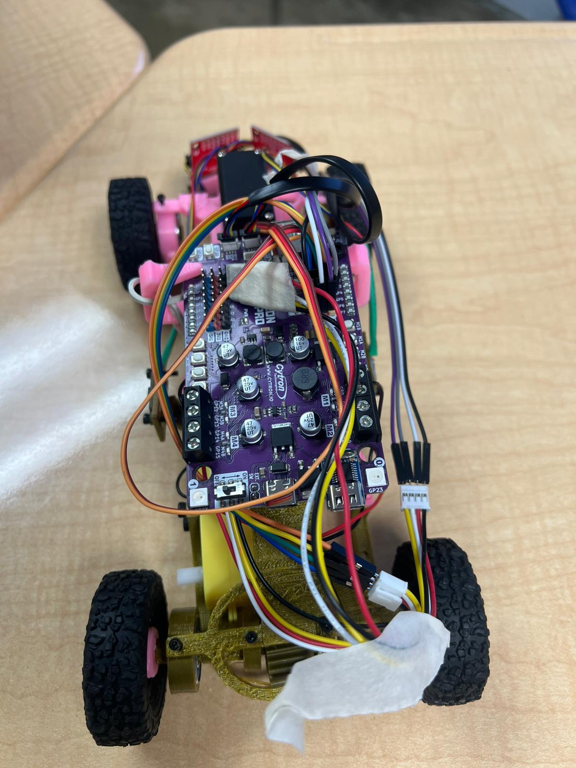
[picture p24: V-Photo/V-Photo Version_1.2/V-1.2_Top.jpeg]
         
  <!-- The Text Overlay -->
  <div style="
    position: absolute; 
    top: 10px; 
    left: 10px; 
    background-color: rgba(0, 0, 0, 0.79); 
    color: white; 
    padding: 8px 12px; 
    font-family: sans-serif;
    border-radius: 10px;">
    <b> Top </b>
  </div>
</div>
        </td>
        <td> <div style="position: relative; display: inline-block;">
        <!-- Image -->
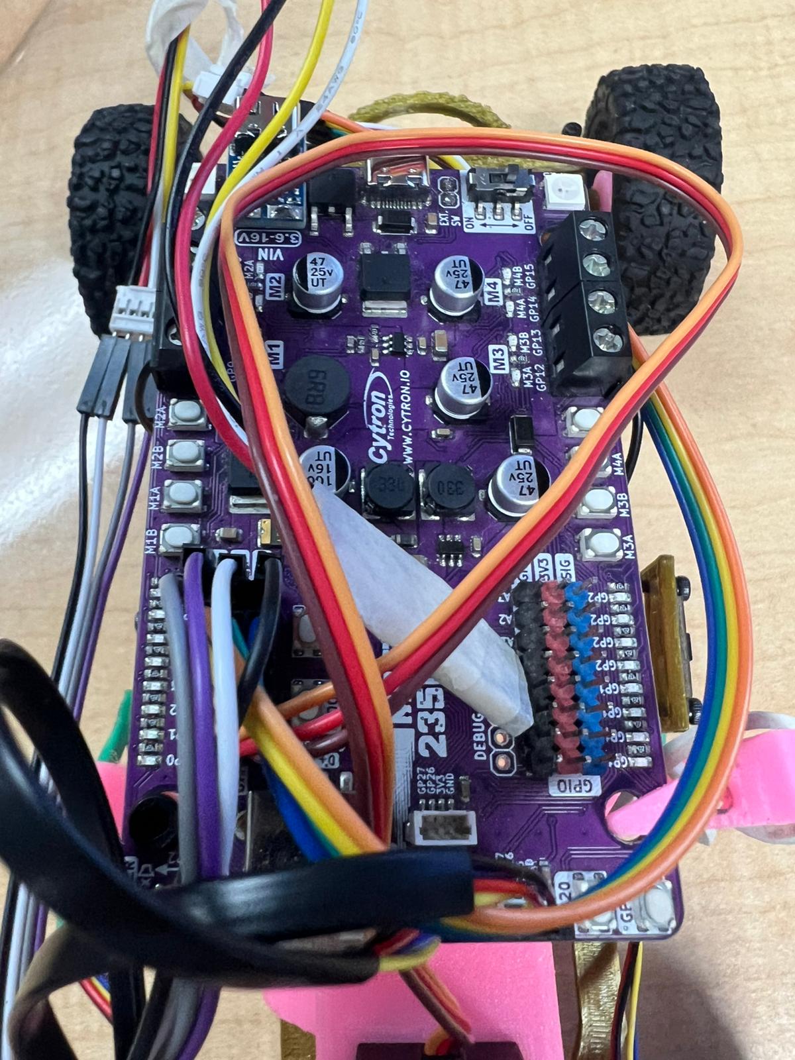
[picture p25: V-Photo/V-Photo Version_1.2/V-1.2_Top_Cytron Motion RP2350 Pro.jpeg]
         
  <!-- The Text Overlay -->
  <div style="
    position: absolute; 
    top: 10px; 
    left: 10px; 
    background-color: rgba(0, 0, 0, 0.79); 
    color: white; 
    padding: 8px 12px; 
    font-family: sans-serif;
    border-radius: 10px;">
    <b> Cytron Motion RP2352 Pro (Microcontroller) </b>
  </div>
</div>
        </td>
    </tr>
    </table>

## V-1.3 (Apr/22/26)
This model is similar to the recent one and is made using 3D-printed materials. It includes two ultrasonic sensors, one on the left and another on the right. The chassis is the same as the previous model, since it performed well. On the top, you can see the battery, and above it is the Cytron Motion RP2350 Pro, where all the data is processed. At the front, there are two TMF8821 sensors used for distance detection, which are programmed along with the color sensors. The new addition is that it also has ultrasonic sensors located beneath the color sensors.

<table>
    <tr> 
        <td> <div style="position: relative; display: inline-block;">
        <!-- Image -->
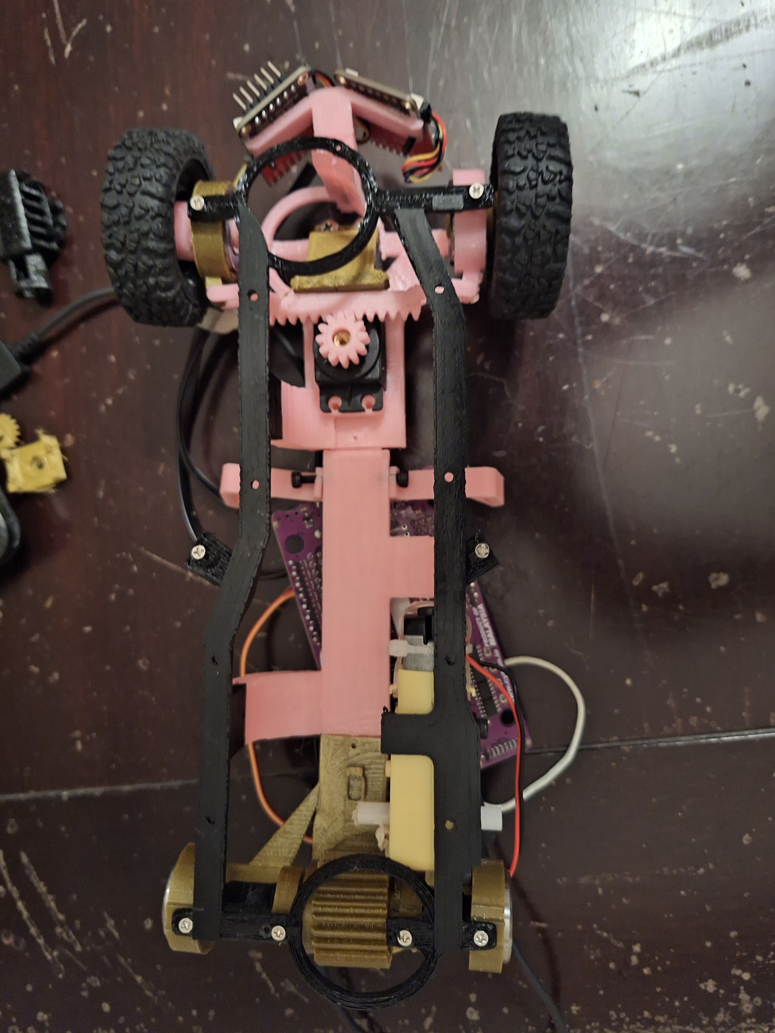
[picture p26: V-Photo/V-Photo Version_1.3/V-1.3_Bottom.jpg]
         
  <!-- The Text Overlay -->
  <div style="
    position: absolute; 
    top: 10px; 
    left: 10px; 
    background-color: rgba(0, 0, 0, 0.79); 
    color: white; 
    padding: 8px 12px; 
    font-family: sans-serif;
    border-radius: 10px;">
    <b> Bottom </b>
  </div>
</div>
        </td> 
        <td> <div style="position: relative; display: inline-block;">
        <!-- Image -->
         Accessibility description
  <!-- The Text Overlay -->
  <div style="
    position: absolute; 
    top: 10px; 
    left: 10px; 
    background-color: rgba(0, 0, 0, 0.79); 
    color: white; 
    padding: 8px 12px; 
    font-family: sans-serif;
    border-radius: 10px;">
    <b> Front </b>
  </div>
</div>
        </td>
        <td> <div style="position: relative; display: inline-block;">
        <!-- Image -->
         Accessibility description
  <!-- The Text Overlay -->
  <div style="
    position: absolute; 
    top: 10px; 
    left: 10px; 
    background-color: rgba(0, 0, 0, 0.79); 
    color: white; 
    padding: 8px 12px; 
    font-family: sans-serif;
    border-radius: 10px;">
    <b> Back </b>
  </div>
</div>
        </td>
    </tr>
    <tr> 
        <td> <div style="position: relative; display: inline-block;">
        <!-- Image -->
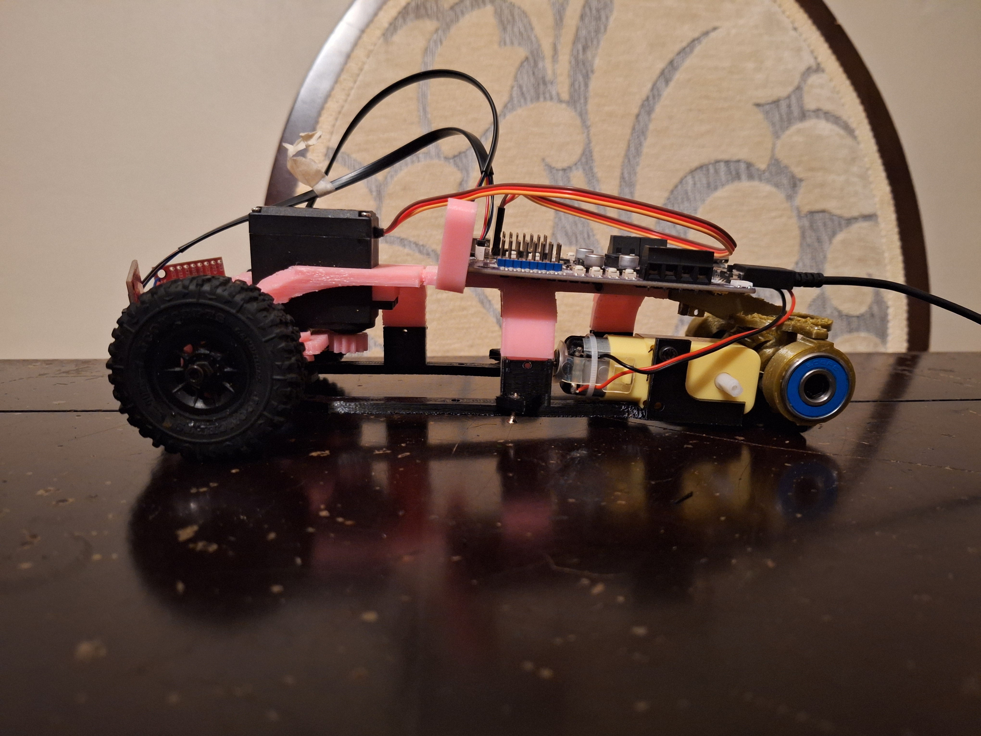
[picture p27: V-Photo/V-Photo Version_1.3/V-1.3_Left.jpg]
         
  <!-- The Text Overlay -->
  <div style="
    position: absolute; 
    top: 10px; 
    left: 10px; 
    background-color: rgba(0, 0, 0, 0.79); 
    color: white; 
    padding: 8px 12px; 
    font-family: sans-serif;
    border-radius: 10px;">
    <b> Left </b>
  </div>
</div>
        </td>
        <td> <div style="position: relative; display: inline-block;">
        <!-- Image -->
         Accessibility description
  <!-- The Text Overlay -->
  <div style="
    position: absolute; 
    top: 10px; 
    left: 10px; 
    background-color: rgba(0, 0, 0, 0.79); 
    color: white; 
    padding: 8px 12px; 
    font-family: sans-serif;
    border-radius: 10px;">
    <b> Top </b>
  </div>
</div>
        </td>
        <td> <div style="position: relative; display: inline-block;">
        <!-- Image -->
         Accessibility description
  <!-- The Text Overlay -->
  <div style="
    position: absolute; 
    top: 10px; 
    left: 10px; 
    background-color: rgba(0, 0, 0, 0.79); 
    color: white; 
    padding: 8px 12px; 
    font-family: sans-serif;
    border-radius: 10px;">
    <b> Right </b>
  </div>
</div>
        </td>
    </tr>
    </table>
    
## V-1.4 (Apr/29/26)

<table>
    <tr> 
        <td> <div style="position: relative; display: inline-block;">
        <!-- Image -->
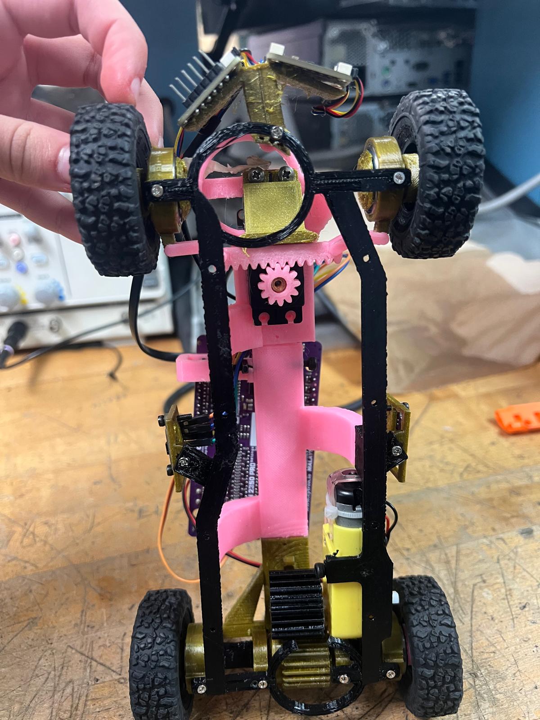
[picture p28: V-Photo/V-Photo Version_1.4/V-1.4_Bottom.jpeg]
         
  <!-- The Text Overlay -->
  <div style="
    position: absolute; 
    top: 10px; 
    left: 10px; 
    background-color: rgba(0, 0, 0, 0.79); 
    color: white; 
    padding: 8px 12px; 
    font-family: sans-serif;
    border-radius: 10px;">
    <b> Bottom </b>
  </div>
</div>
        </td> 
        <td> <div style="position: relative; display: inline-block;">
        <!-- Image -->
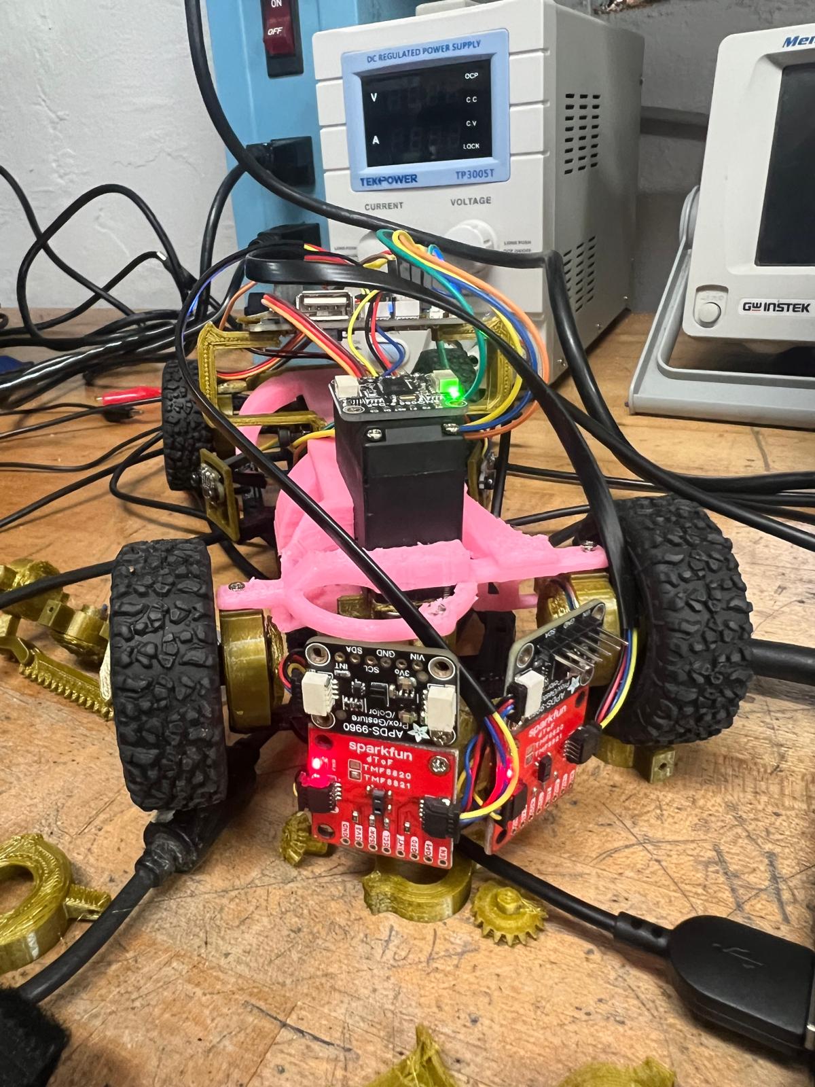
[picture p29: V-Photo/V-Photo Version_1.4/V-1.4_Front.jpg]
         
  <!-- The Text Overlay -->
  <div style="
    position: absolute; 
    top: 10px; 
    left: 10px; 
    background-color: rgba(0, 0, 0, 0.79); 
    color: white; 
    padding: 8px 12px; 
    font-family: sans-serif;
    border-radius: 10px;">
    <b> Front </b>
  </div>
</div>
        </td>
       <td> <div style="position: relative; display: inline-block;">
        <!-- Image -->
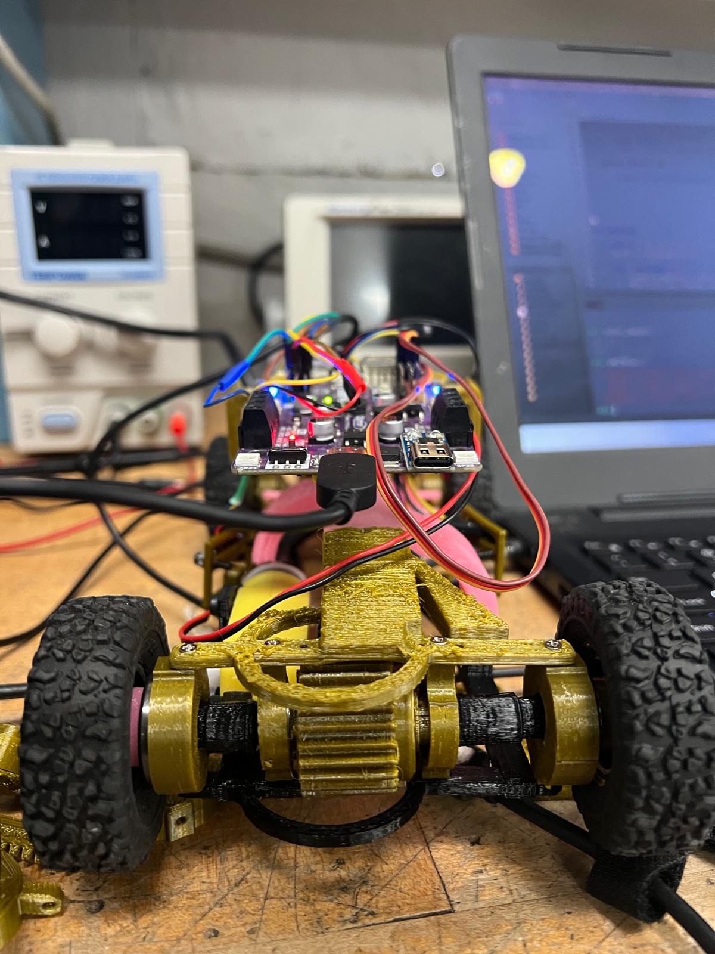
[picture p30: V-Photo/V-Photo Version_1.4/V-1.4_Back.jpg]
         
  <!-- The Text Overlay -->
  <div style="
    position: absolute; 
    top: 10px; 
    left: 10px; 
    background-color: rgba(0, 0, 0, 0.79); 
    color: white; 
    padding: 8px 12px; 
    font-family: sans-serif;
    border-radius: 10px;">
    <b> Back </b>
  </div>
  </div>
</div>
        </td>
    </tr>
    <tr> 
        <td> <div style="position: relative; display: inline-block;">
        <!-- Image -->
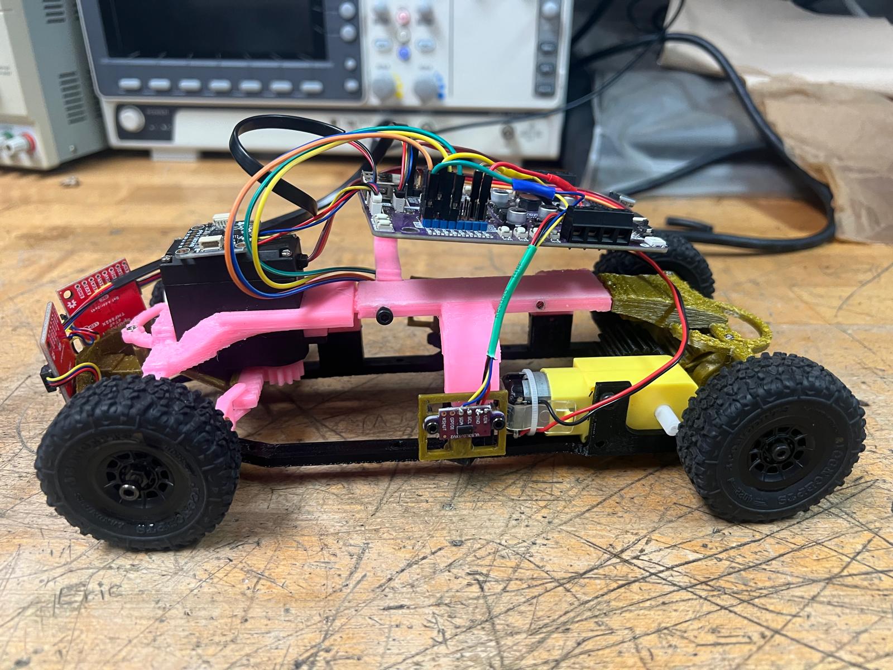
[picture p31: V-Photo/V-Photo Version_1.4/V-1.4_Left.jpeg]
         
  <!-- The Text Overlay -->
  <div style="
    position: absolute; 
    top: 10px; 
    left: 10px; 
    background-color: rgba(0, 0, 0, 0.79); 
    color: white; 
    padding: 8px 12px; 
    font-family: sans-serif;
    border-radius: 10px;">
    <b> Left </b>
  </div>
</div>
        </td>
        <td> <div style="position: relative; display: inline-block;">
        <!-- Image -->
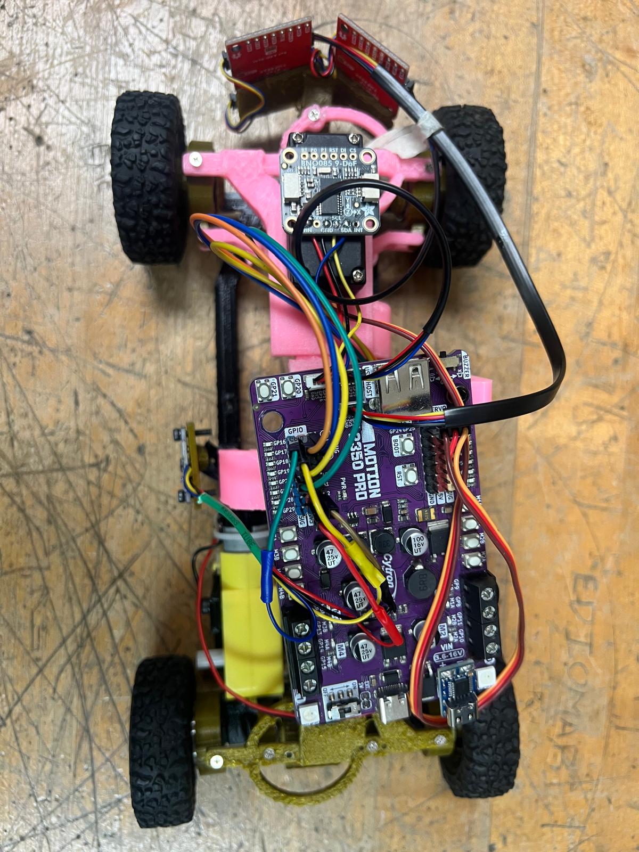
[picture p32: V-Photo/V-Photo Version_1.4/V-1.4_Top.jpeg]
         
  <!-- The Text Overlay -->
  <div style="
    position: absolute; 
    top: 10px; 
    left: 10px; 
    background-color: rgba(0, 0, 0, 0.79); 
    color: white; 
    padding: 8px 12px; 
    font-family: sans-serif;
    border-radius: 10px;">
    <b> Top </b>
  </div>
</div>
        </td>
        <td> <div style="position: relative; display: inline-block;">
        <!-- Image -->
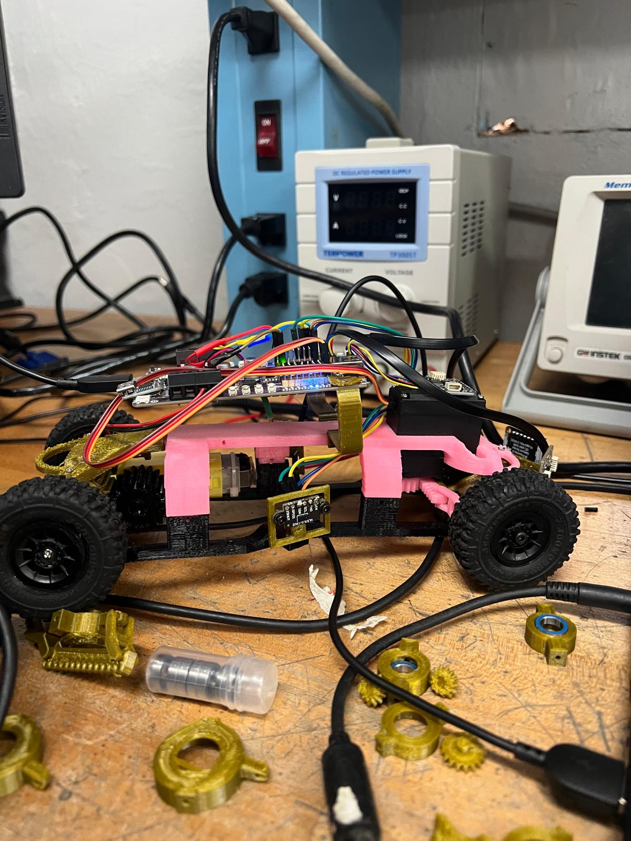
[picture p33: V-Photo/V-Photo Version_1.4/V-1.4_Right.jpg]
         
  <!-- The Text Overlay -->
  <div style="
    position: absolute; 
    top: 10px; 
    left: 10px; 
    background-color: rgba(0, 0, 0, 0.79); 
    color: white; 
    padding: 8px 12px; 
    font-family: sans-serif;
    border-radius: 10px;">
    <b> Right </b>
  </div>
</div>
        </td>
    </tr>
    </table>

## V-1.5 (Sept/12/26)

<table>
    <tr> 
        <td> <div style="position: relative; display: inline-block;">
        <!-- Image -->
         Accessibility description
  <!-- The Text Overlay -->
  <div style="
    position: absolute; 
    top: 10px; 
    left: 10px; 
    background-color: rgba(0, 0, 0, 0.79); 
    color: white; 
    padding: 8px 12px; 
    font-family: sans-serif;
    border-radius: 10px;">
    <b> Bottom </b>
  </div>
</div>
        </td> 
        <td> <div style="position: relative; display: inline-block;">
        <!-- Image -->
         Accessibility description
  <!-- The Text Overlay -->
  <div style="
    position: absolute; 
    top: 10px; 
    left: 10px; 
    background-color: rgba(0, 0, 0, 0.79); 
    color: white; 
    padding: 8px 12px; 
    font-family: sans-serif;
    border-radius: 10px;">
    <b> Front </b>
  </div>
</div>
        </td>
       <td> <div style="position: relative; display: inline-block;">
        <!-- Image -->
         Accessibility description
  <!-- The Text Overlay -->
  <div style="
    position: absolute; 
    top: 10px; 
    left: 10px; 
    background-color: rgba(0, 0, 0, 0.79); 
    color: white; 
    padding: 8px 12px; 
    font-family: sans-serif;
    border-radius: 10px;">
    <b> Back </b>
  </div>
  </div>
</div>
        </td>
    </tr>
    <tr> 
        <td> <div style="position: relative; display: inline-block;">
        <!-- Image -->
         Accessibility description
  <!-- The Text Overlay -->
  <div style="
    position: absolute; 
    top: 10px; 
    left: 10px; 
    background-color: rgba(0, 0, 0, 0.79); 
    color: white; 
    padding: 8px 12px; 
    font-family: sans-serif;
    border-radius: 10px;">
    <b> Left </b>
  </div>
</div>
        </td>
        <td> <div style="position: relative; display: inline-block;">
        <!-- Image -->
         Accessibility description
  <!-- The Text Overlay -->
  <div style="
    position: absolute; 
    top: 10px; 
    left: 10px; 
    background-color: rgba(0, 0, 0, 0.79); 
    color: white; 
    padding: 8px 12px; 
    font-family: sans-serif;
    border-radius: 10px;">
    <b> Top </b>
  </div>
</div>
        </td>
        <td> <div style="position: relative; display: inline-block;">
        <!-- Image -->
         Accessibility description
  <!-- The Text Overlay -->
  <div style="
    position: absolute; 
    top: 10px; 
    left: 10px; 
    background-color: rgba(0, 0, 0, 0.79); 
    color: white; 
    padding: 8px 12px; 
    font-family: sans-serif;
    border-radius: 10px;">
    <b> Right </b>
  </div>
</div>
        </td>
    </tr>
    </table>

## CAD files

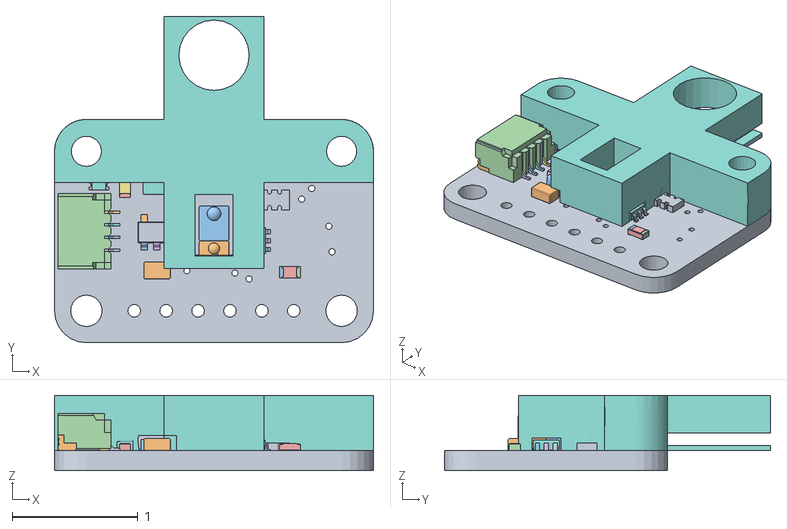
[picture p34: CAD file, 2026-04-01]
Electrical-Design/HardwareCADS/APDS LENS.obj
2.54 x 2.60 x 0.6

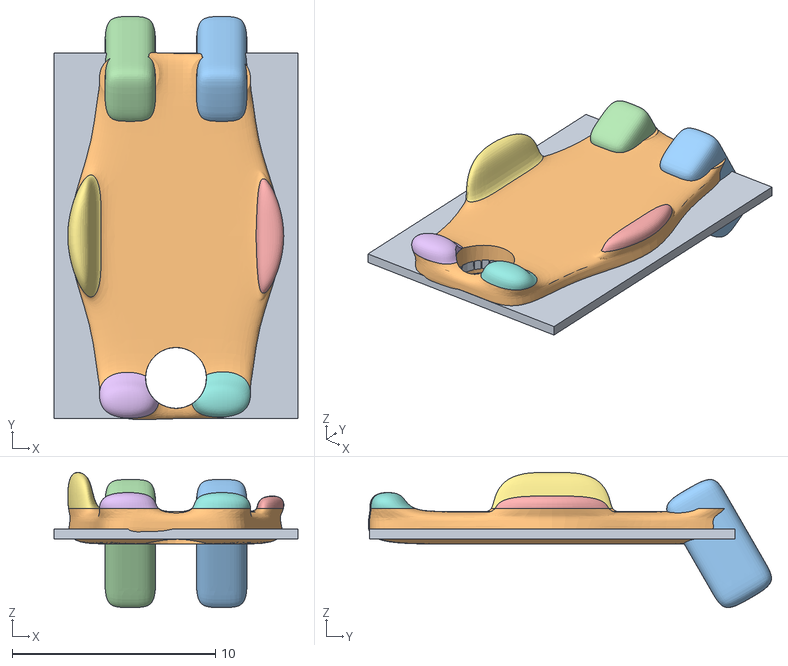
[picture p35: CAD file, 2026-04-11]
Mechanics/CAD/Full-Models/exp.obj
12.0 x 19.8 x 6.65

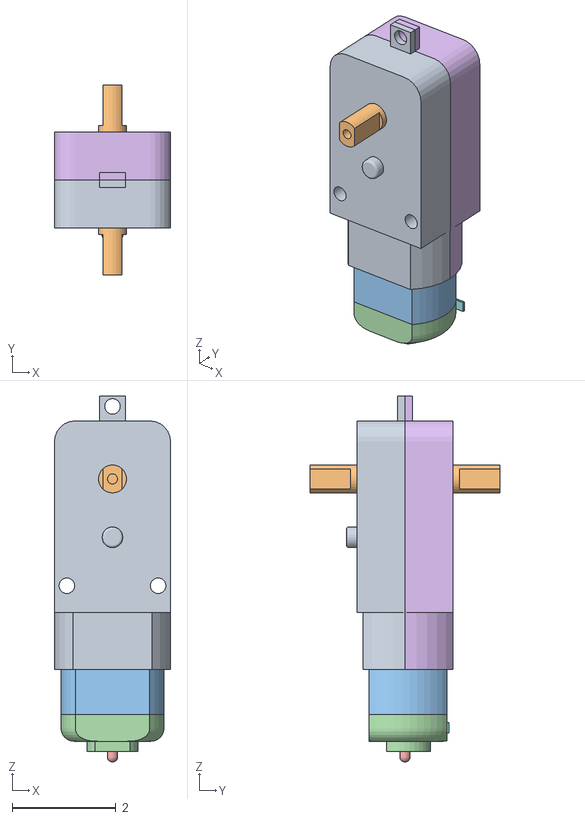
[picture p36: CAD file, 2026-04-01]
Electrical-Design/HardwareCADS/3777 TT Motor.obj
2.24 x 3.66 x 7.06

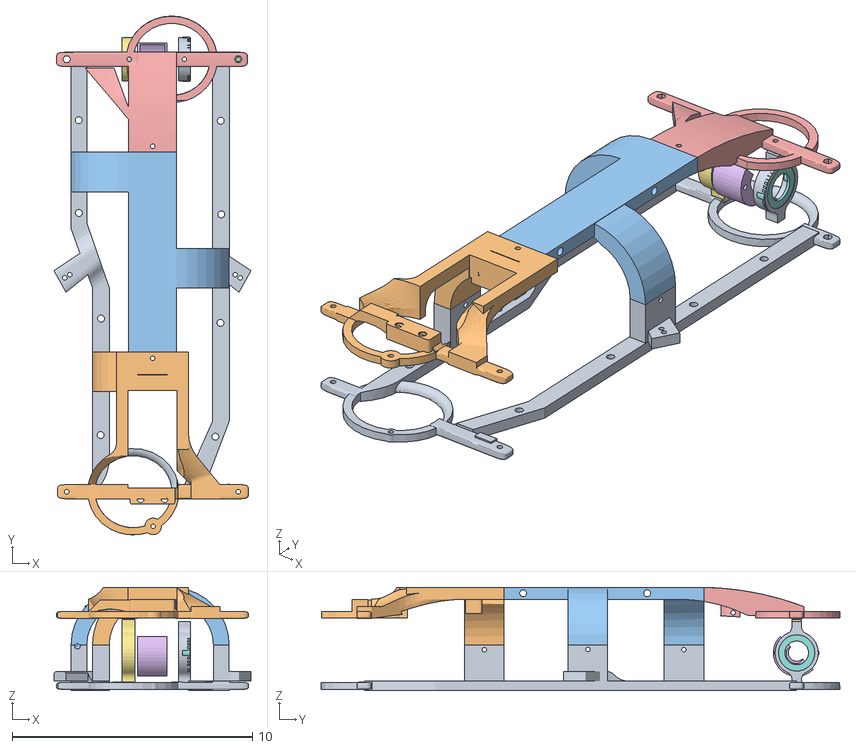
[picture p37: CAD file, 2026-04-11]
Mechanics/CAD/Full-Models/exp50.obj
8.20 x 21.6 x 4.30

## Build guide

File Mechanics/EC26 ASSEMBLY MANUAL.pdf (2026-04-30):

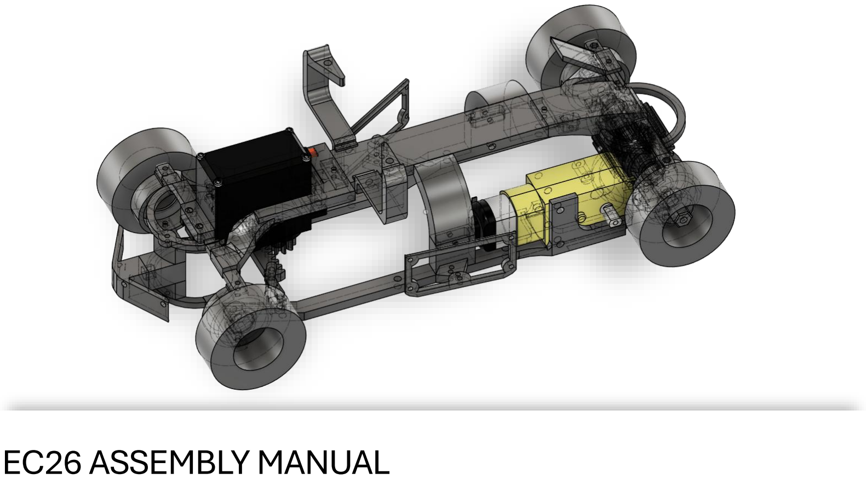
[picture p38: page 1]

# EC26 ASSEMBLY MANUAL

To assemble this vehicle you will need specific tools like M2 & M3 screws and screwdrivers depending on your screw choice. Also you will need a fdm printer. we recommend using PETG since is the material we used and proved to be effective. Last but not least you may need some basic knowledge on 3d manufacturing as tolerances may vary between

printers and parts may not fit well.

# TABLE OF CONTENTS

1. FRONT UPPER CHASSIS
2. FRONT BEARING L
3. STEERING PINION
4. RACK TO WHEEL JOINT
5. RACK
6. FRONT BEARING R
7. AXLE GEAR
8. SPIDER GEAR
9. SPIDER GEAR JOINT
10. DIFFERENTIAL TO AXLE JOINT L
11. DIFFERENTIAL TO AXLE JOINT R
12. DIFFERENTIAL INNER CASE
13. SERVO MOTOR (MG996R)
14. TT MOTOR
15. CYTRON MOTION PRO RP2350
16. FRONT SENSOR HUB
17. REAR AXLE L
18. WHEEL HUB
19. UPPER CHASSIS
20. MCU & BATTERY HOLDER
21. REAR BEARING
22. DIFFERENTIAL DRIVE GEAR
23. LOWER CHASSIS
24. REAR AXLE R
8. to 13: Front assembly (steering system)
14. to 24: Rear assembly (differential & rear axles)

25 to 30: Chassis (chassis, hardware mounts and power drive

1. to 4. Parts needed for assembly:

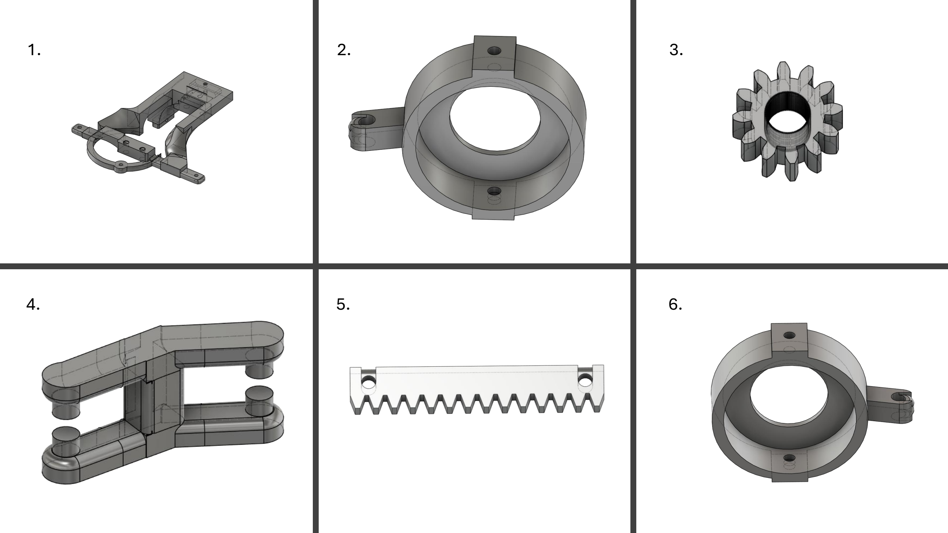
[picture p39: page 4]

1. | 2. | 3.
4. | 5. | 6.

7. | 8. | 9.
10. | 11. | 12.

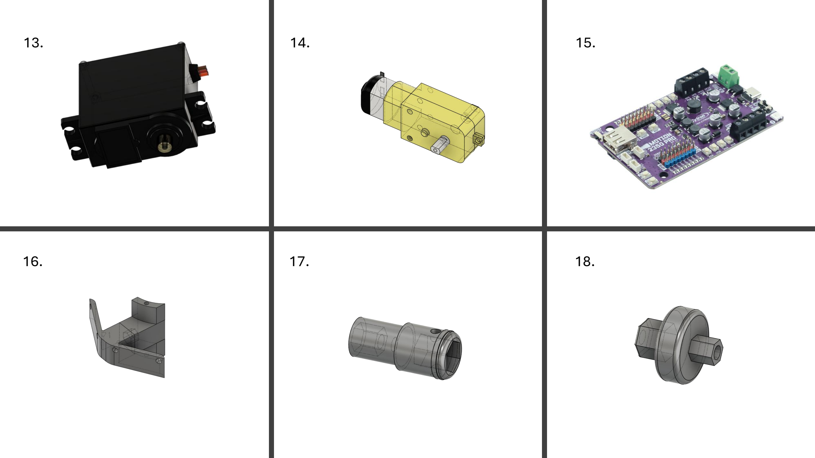
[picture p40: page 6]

13. | 14. | 15.
16. | 17. | 18.

13. | 14. | 15.
16. | 17. | 18.

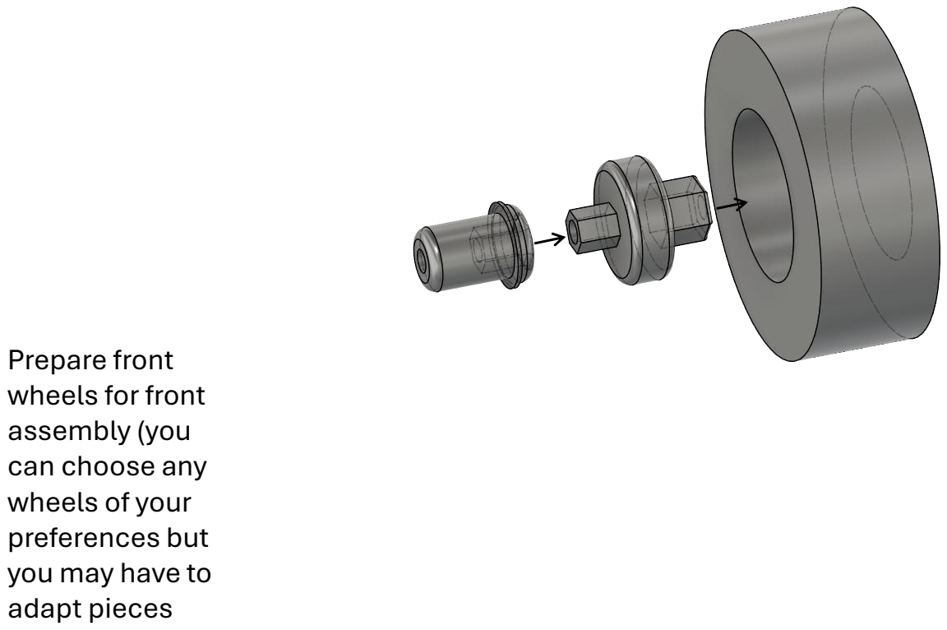
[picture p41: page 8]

Prepare front
wheels for front
assembly (you
can choose any
wheels of your
preferences but
you may have to
adapt pieces

Joint front
bearings with the
rack joint (x2)

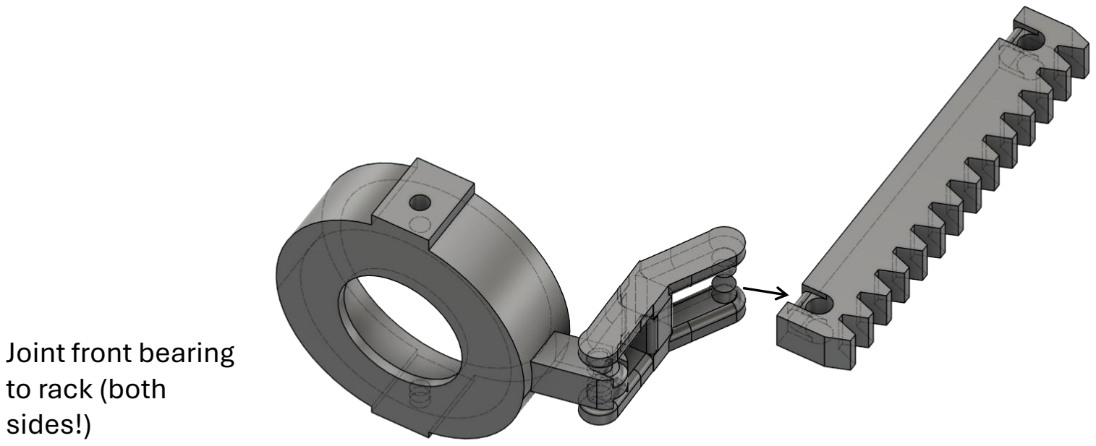
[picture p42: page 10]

Joint front bearing
to rack (both
sides!)

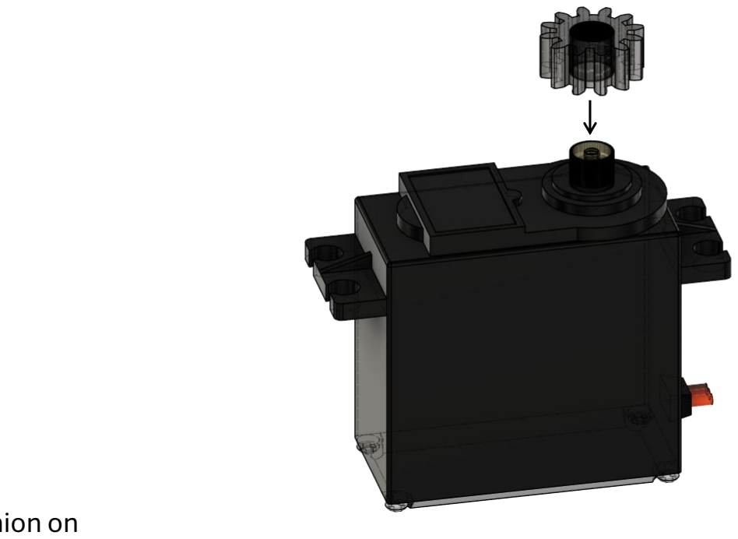
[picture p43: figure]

Insert pinion on
MG996R servomotor

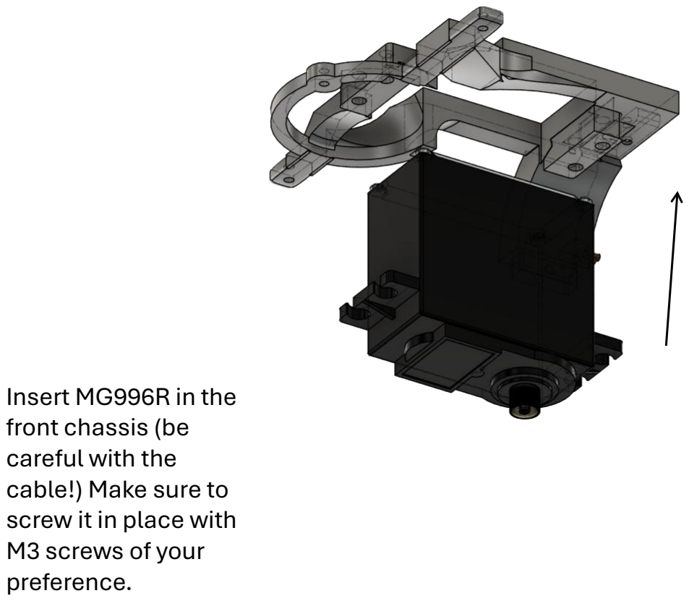
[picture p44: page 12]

Insert MG996R in the
front chassis (be
careful with the
cable!) Make sure to
screw it in place with
M3 screws of your
preference.

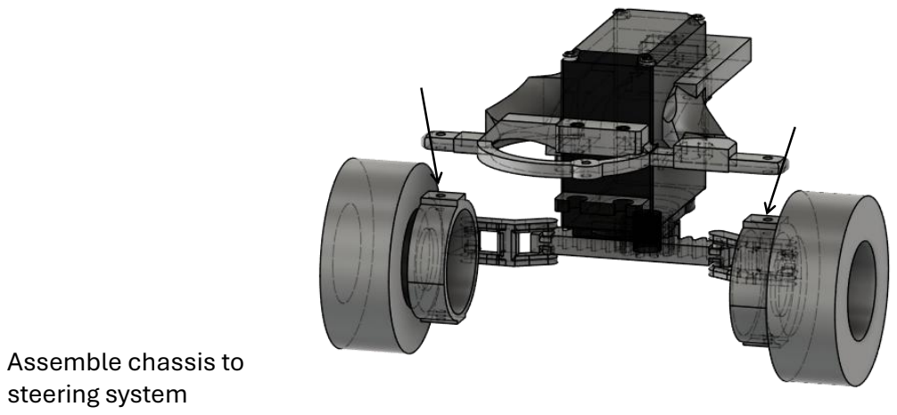
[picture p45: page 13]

Assemble chassis to
steering system

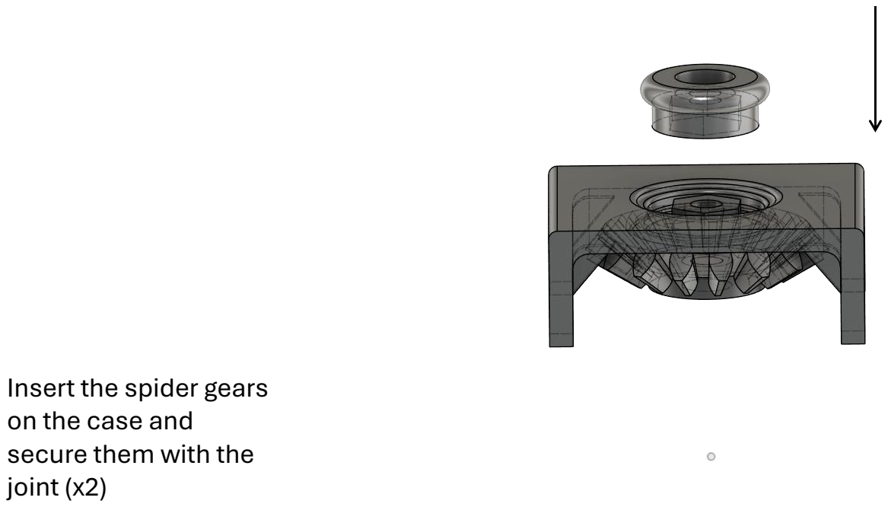
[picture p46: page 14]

Insert the spider gears
on the case and
secure them with the
joint (x2)

Hold pinion on the
differential assembly
(both sides).

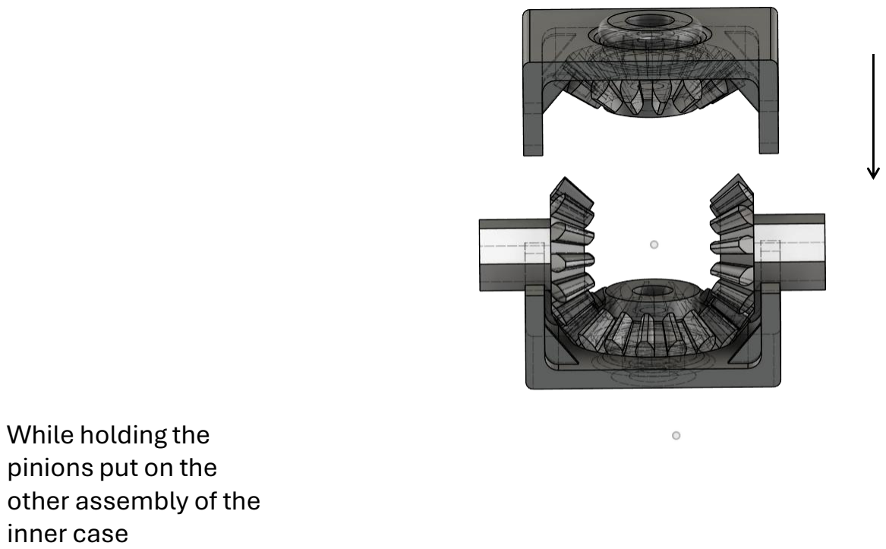
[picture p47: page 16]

While holding the
pinions put on the
other assembly of the
inner case

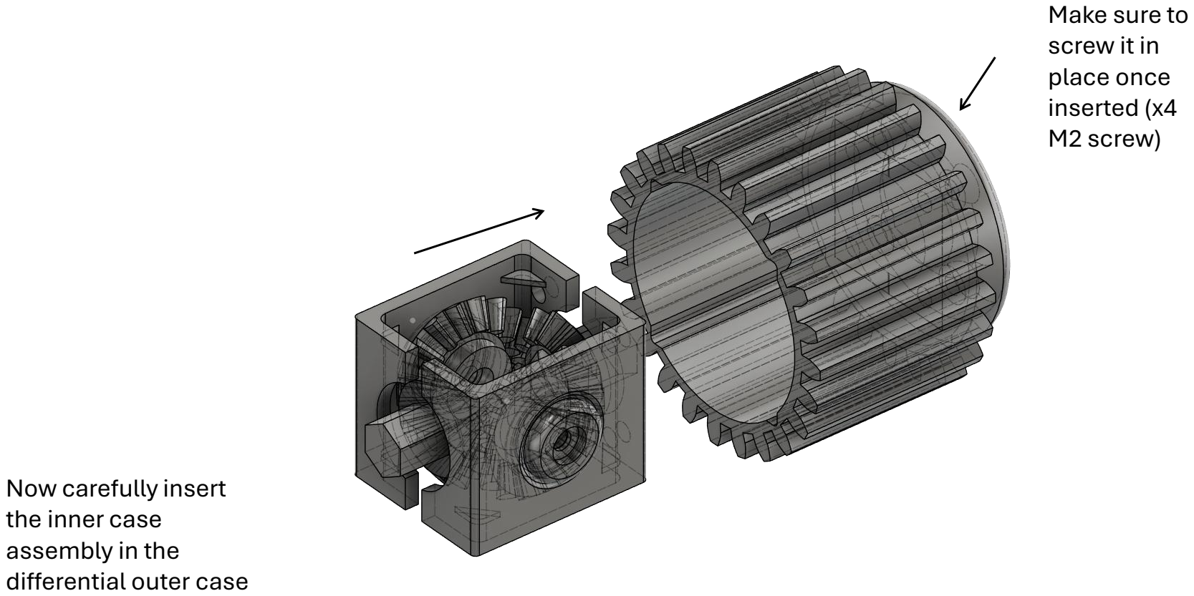
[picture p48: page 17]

Now carefully insert
the inner case
assembly in the
differential outer case

Make sure to
screw it in
place once
inserted (x4
M2 screw)

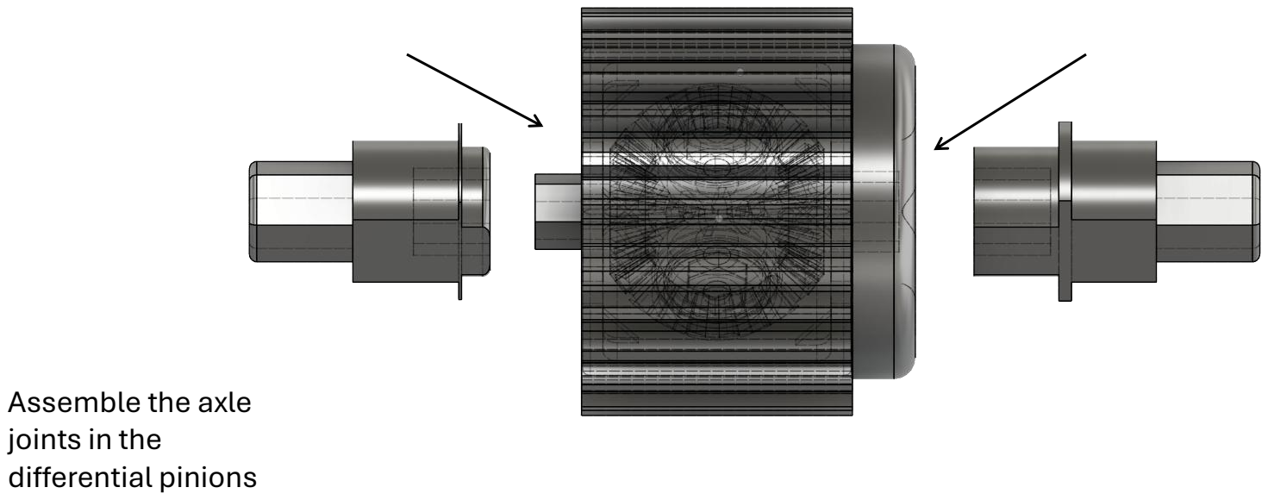
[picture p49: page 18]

Assemble the axle
joints in the
differential pinions

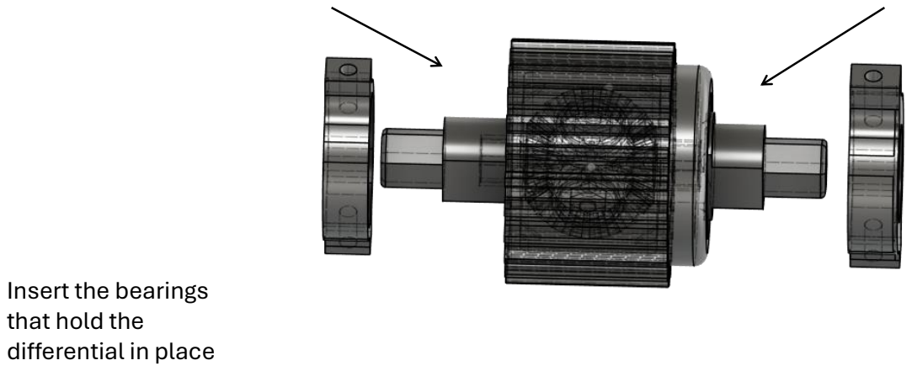
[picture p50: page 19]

Insert the bearings
that hold the
differential in place

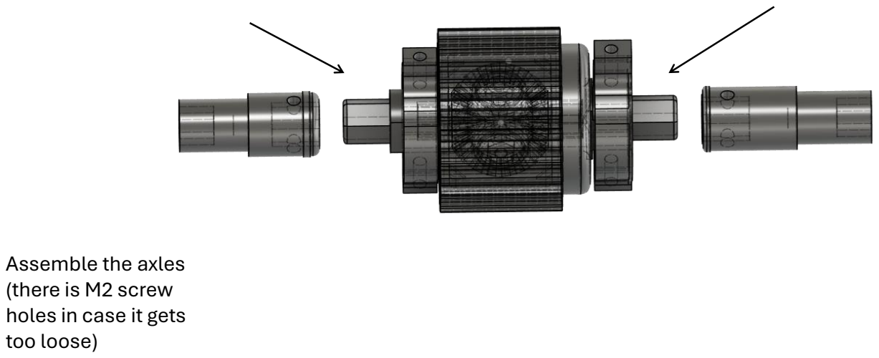
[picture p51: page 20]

Assemble the axles
(there is M2 screw
holes in case it gets
too loose)

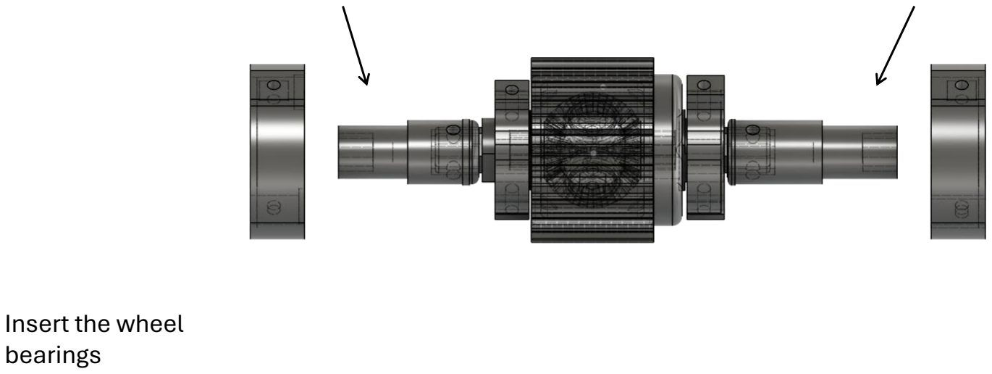
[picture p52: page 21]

Insert the wheel
bearings

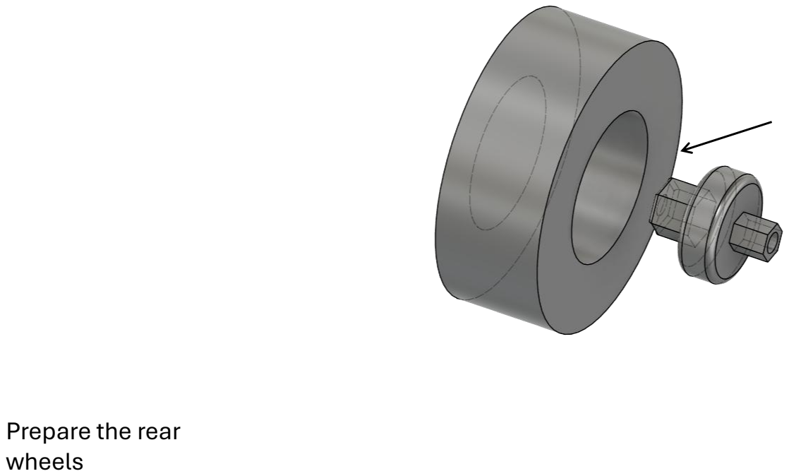
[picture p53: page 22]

Prepare the rear
wheels

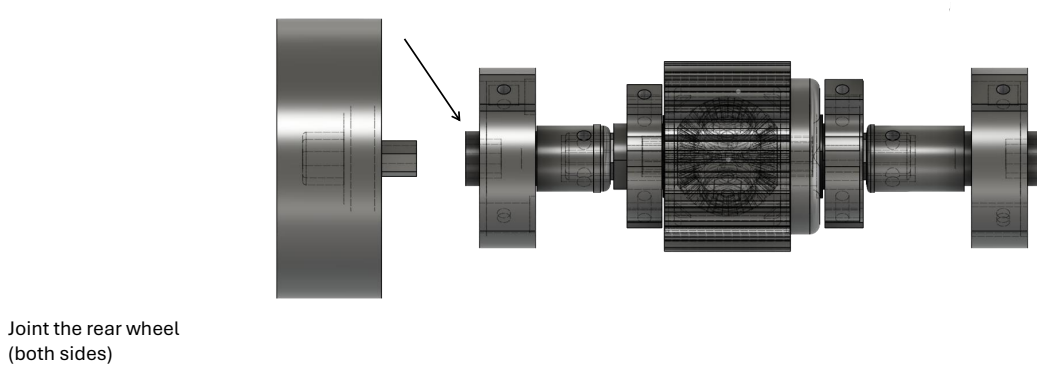
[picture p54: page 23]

Joint the rear wheel
(both sides)

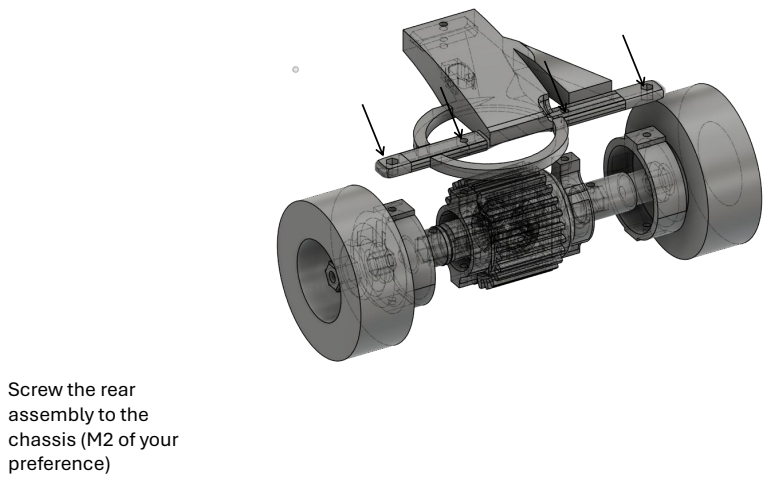
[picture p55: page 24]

Screw the rear
assembly to the
chassis (M2 of your
preference)

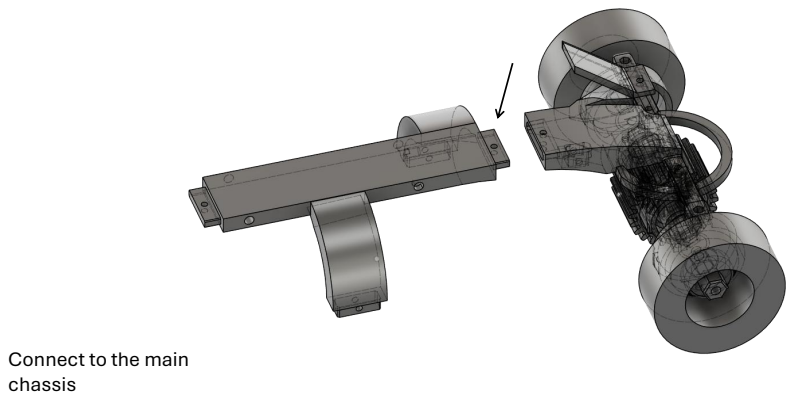
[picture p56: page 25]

Connect to the main
chassis

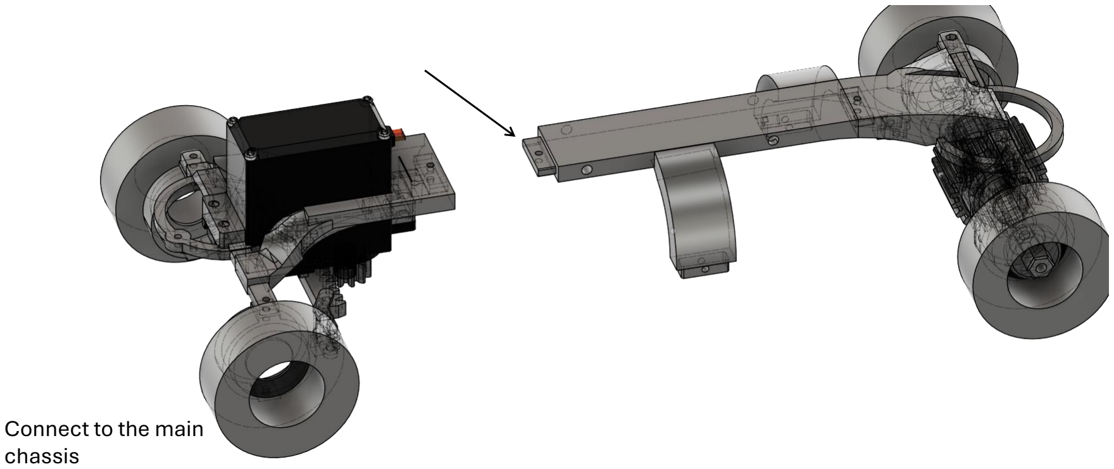
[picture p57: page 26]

Connect to the main
chassis

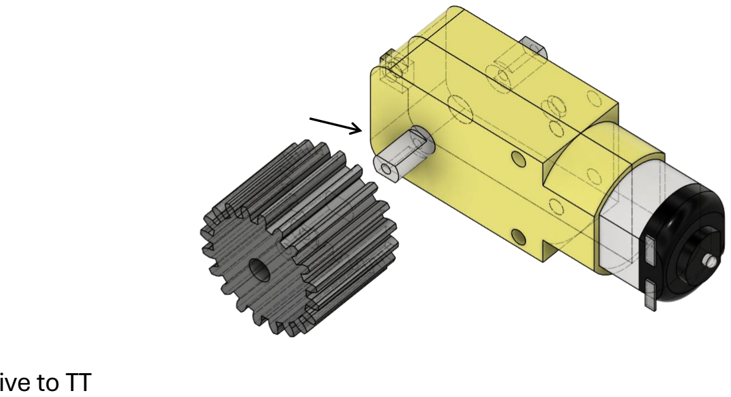
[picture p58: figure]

Joint power drive to TT
motor

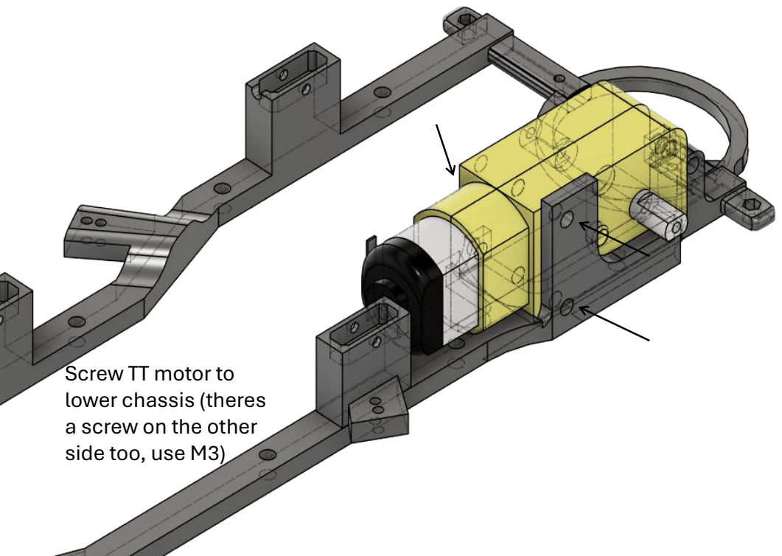
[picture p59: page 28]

Screw TT motor to
lower chassis (theres
a screw on the other
side too, use M3)

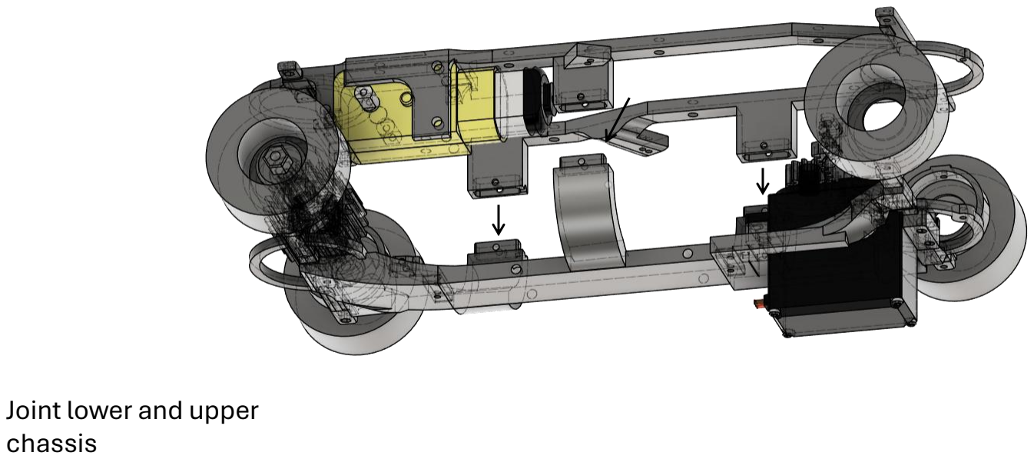
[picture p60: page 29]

Joint lower and upper
chassis

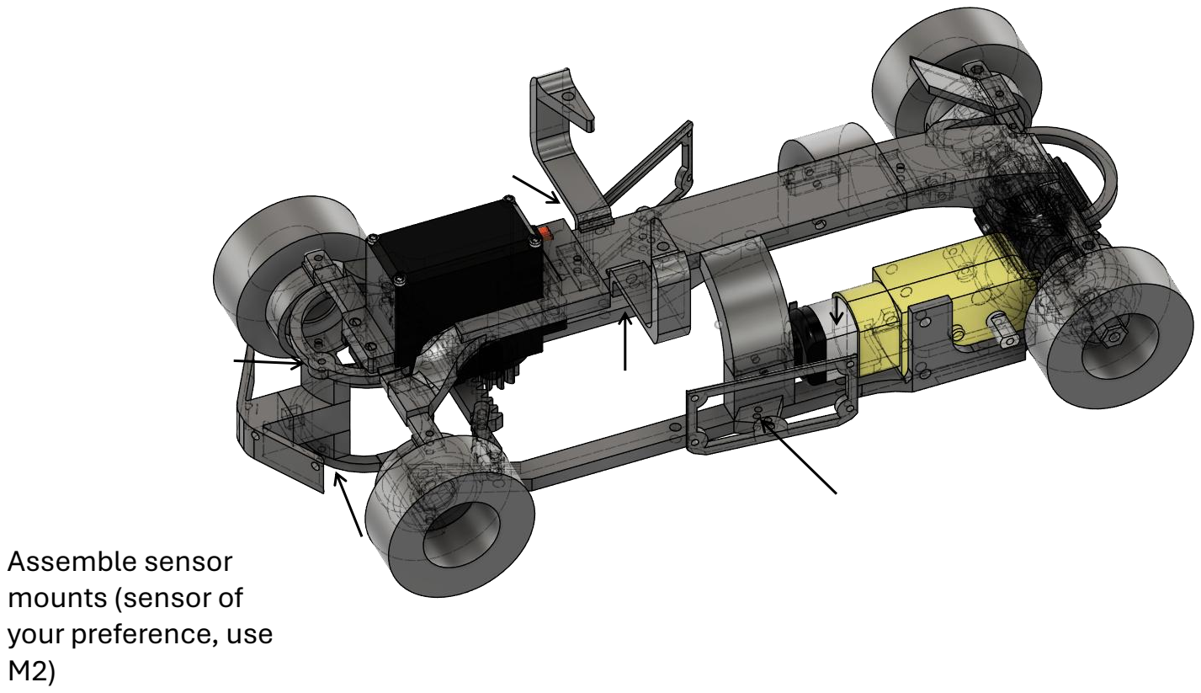
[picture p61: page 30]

Assemble sensor
mounts (sensor of
your preference, use
M2)

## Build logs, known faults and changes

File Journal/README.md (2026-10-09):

# Journal
In this file you will find our group process of our date a base work and our progress and growth.

## Competitions
- Feb/21/26 - We had our 1st competition. Landing on first place. We had a lot of complications, starting of with the track it was incomplete that made things harder. Our sensor weren't working either. The scores being equal: 
    * First Round: 0
    * Second Round: 27
    * Third Round (with obstacles): 4

- Mar/28/26 - On March 28, we participated in our second Future Engineers tournament, which took place at Robinson School. From the start of the day, we faced several difficulties. Before going out to compete, our team had a problem due to a lack of communication among ourselves. By mistake, we forgot the infrared sensor, which was the main sensor we were going to use, along with its corresponding MCU. Fortunately, we still had the sound sensors, which were the older method we had used previously, along with their MCU.
During the trip to Robinson School, I was working on the robot’s programming, trying to at least get it to execute some basic function for the competition.
When we arrived at the venue, we first went through the registration process. After that, we had the official welcome for the event, and once it ended, we went to our work tables in the competition area. There, we were given approximately 40 minutes for maintenance and programming.
During that time, we managed to get the robot to move, but it had several issues. The differential was failing, which affected its movement. While I was trying to program and test the sound sensors, an internal error appeared in the code that prevented it from being properly analyzed, and the program was also unable to detect the robot. Because of this, I couldn’t continue working on that part of the programming.
Given the situation, I decided to simplify the strategy: make the robot move only in a straight line. To try to make it turn correctly, I manually adjusted the front wheels, tilting them slightly in the hope that the robot could turn without touching the walls of the track.
In the first round, the robot did not move very well and took time to start, but it still managed to complete four sections of the course before hitting a corner.
Then we had an additional 20 minutes for maintenance and programming. During that time, we tried to better adjust the tires so the robot could go beyond four sections.
Before the second round, we had an Open Challenge. The challenge consisted of throwing a piece of paper so that it would land in the center of a designated area. The selected twist was that the center square would become a rectangle.
However, when it was time to run the robot in the second round, it did not start because the differential failed completely. As a result, we got a score of 0 in that round.
After that, we were given 40 more minutes for maintenance and programming. Since the programming was still causing problems, we attempted a mechanical solution: we placed tape on the differential to try to stabilize it. This worked a little, and the car was able to move again, although not perfectly.
The third round included obstacles. Each team member could place one obstacle on the course, while the opponents also placed theirs. When it was time to run the robot, it did not work because the pieces of tape we had placed on the differential came loose.
In the fourth round, we tried the same solution, but the result was the same, and once again we scored 0 points.
At the end of all the rounds, we finished with a total of 4 points, which placed us in fourth place in the competition.
Although this experience was frustrating, it was also a great learning opportunity. Despite the problems, we never gave up. Additionally, I had to compete alongside my brother because my teammates had other commitments. It was not easy, but this experience left me highly motivated to improve in the next competition.
We learned that we need to work more on team communication, better organization before competitions, and improving the design and reliability of the robot.

##

* Jan/14/26 - The group was created. We gather some ideas with the brainstorm method. One of the ideas were: a compass for reduce the comusme of time for the robot to know where's located.

* Jan/20/26 - Gather some information of the old models.

    * One of them being made November 25, 2024. This model was made out of LEGOS. It was a square that it wasn't very functional because it was large.

    * Other one being made on October 19, 2025. This one was made of 3D print materials. This model took time for it to work but it failed because it was too complex to work (it was 4x4 model). 

    * The actual car model was created on December 22, 2025. This one was also made of 3D print materials. With the past knowledge of vehicles models, it decided to be a smaller model for it to manage best the track, with two sensors in front for it to read the colors of the obstacles (2 APDS9960). 

* From this point on we're going to talk about the progress of this model and progress the team. 

* Jan/21/26 - We review the rules and wrote the ones we thought were more important. 

* Jan/22/26 - We started of viewing a video of microphyton. The mechanic team member started creating a new piece for the readings to be more accurate. We took a brief class of how to program lights (turn on and off). 

* Jan/24/26 - We continued with the process of creating the piece for the accurate readings.

* Jan/27/26 - Our coach explained us what github was and how to use it.

* Jan/30/26 - The piece for the accurate reading was finally printed. 

* Feb/04/26 - We stablish the roles of each member and the programmer was learning how to. 

* Feb/05/26 - We trying to figure out how to make the vehicle park.

* Feb/18/26 - We eliminated the APDS9960 because we weren't be using it for the competition of February 21.

* Feb/21/26 - Competitions!

* Feb/24/26 - We were working on the documentation.

* Mar/04/26 - After the results of the competition we fixed some problems that we saw. One of them being: 
    * The movility of the front wheels be fixed with a league.

* Mar/26/26 - 3D printed the bevel gear. Changed the old for the new bevel gear.

* Mar/28/26 - Competitions!

* Apr/01/26 - We worked on all the program. The programator worked on the color readings. The mechanic was making a piece for the vehicle to be sustainable.

* Apr/02/26 - We tested out the program we work on yesterday on the track. After testing worked more on the program.

* Apr/07/26 - We work on the program and while working on it a Pin of one connector broked. So, the mechanic fixed it (the errors that appeared on the program were ERROR 19 and E10)

* Apr/11/26 - Our team worked on the GitHub having it updated on the process. We were having daily (weekly). Also we were fixing the 3D printer and gathering ideas for a new model (focusing on improving the parking).

* Apr/13/26 - We were making a new design with the ideas of April 11, being focused on the parking.

* Apr/14/26 - Today we also were working on the Github making sure we have everything we offer updated, of the new design we were printing the chassis it ended up failing after multiple tries. But we are looking forward to try it again.

* Apr/15/26 - Today we are continuing with the Github and printed a new chassis the reason for this is for the differential its slighly bigger now.

* Apr/21/26 - Today we are working on the Github and also we took pictures together as a group.

* Apr/24/26 - Today we assemble the APDS9960 distance sensors, we are also working on documentation and we also practice on the track.

* Apr/25/26 - Today we tested the robot while programming and an issue was presented. The robot is poorly rotating the way it should. Were hoping to fix it.

* Apr/28/26 - Today, we adjusted the wheels because they came apart while we were practicing on the track on the 25th of this month. Even though it only happened once, we made sure to secure them properly to prevent the issue from happening again. We also worked on the GitHub(car). For the next meeting we are looking forward to the wheels staying in place and performing well.

* Apr/29/26 - Today, we started by practicing on the track. We recorded a video of the vehicle completing the track for our GitHub. We also worked on adding more information to the GitHub.We made good progress the robot now stops when it detects walls and can complete laps. We are looking forward to improving the color detection so the vehicle can perform better on the track.

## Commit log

2026-03-27 First push
    here we uploaded the first working codes and some cad models of our main sensors, this sensors may be changed for stronger ones later on and the codes are prototype ones and will be upgraded
    [3777 TT Motor.obj, APDS LENS.obj]
2026-04-11 UPLOAD OF FULL MODELS
    Here we are uploading our full cad models as for now, we decided it was best to upload models that were 10 version appart as every 10 updates you can see real progress made. From the first model to t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
    [exp.obj, exp50.obj]
2026-04-14 Reorganize Readme
    [exp.obj, exp50.obj]
2026-04-15 Organization and introducction
    In this push we organized more the github and writed a introduction to our git ^_^
    [3777 TT Motor.obj, APDS LENS.obj, exp.obj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]
2026-04-30 Big update
    [3777 TT Motor.obj, APDS LENS.obj]
2026-04-30 This are the instrucctions of how to assemble our car
2026-04-30 This is the schematic for the sensor we are designing
    This schematic consists of a mix of the sensors tmf8821 and tcs34001fnn but its compatible with other sensors from either the tmf and tcs series, this will be a single pcb for both sensors and we wil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
    [TMF-TCS.kicad_sch]
